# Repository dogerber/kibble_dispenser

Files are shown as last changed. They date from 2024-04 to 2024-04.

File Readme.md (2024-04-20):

# Kibble Dispenser

splash

## Purpose

This device is meant to automatically dispense cat treats to keep cats active during the day. Treats are placed in the small compartments and randomly dispensed within a given time frame.

## Materials

- Arduino UNO
- Adafruit Motorshield V2 (Probably possible without it though)
- 3d Printed parts
- DC Motor
- Power adapter
- [TCRT5000](https://www.bastelgarage.ch/infrarot-sensor-tcrt5000-naherungsschalter-breakout-modul) IR Sensor
- [OLED Display Blau I2c 128x32 0.91’’](https://www.bastelgarage.ch/oled-display-blau-i2c-128x32-0-91?search=ssd13)
- (optional) Buzzer
- resistors, buttons, wires

## How to build

- 3D print all parts from [/dispenser](/dispenser/)
- laser cut and glue enclosure from [/enclosure](/enclosure/)
- install the necessary libraries (see [Dependencies](#dependencies))
- adjust parameters in the code
- wire everything according to [wiring](#wiring)
- upload code/`code.ino`to Arduino Uno
- adjust TCRT5000 potentiometer, such that it triggers when a kibble falls down, but not when something further away moves

### Wiring

- Button 1 to D11 (with pulldown resistor)
- Button 2 to D12 (with pulldown resistor)
- Display to SDA and SCL
- IR sensor TCRT5000 (digital D0) to D2 (used for interrupt)
- (optional) Buzzer to D9
- DC Motor to M1 port of the Motorshield

## How to use

- Update parameters in the code to fit your preferences.
- Manual kibble dispensing is possible with `button2`
- To reset the dispenser push `button1`

## Different Dispensing Mechanisms

To exactly dispense one kibble each time the machine is triggered was harder than expected. For future reference I'm quickly summarizing all the failed approaches here.

(Pictures below)

From top to bottom:

- Final design and only one to work reliably. Unfortunately, the kibbles need to be placed one by one
- Using a feeding wheel like this was very unreliable. It would often not pickup anything
- The auger screw worked sometimes, but often the kibbles would make clogs in the screw that would dispense all together. Redimensioning to make it smaller lead to a lot of jamming problems.
- Inspired by [mint-dispenser](https://www.google.com/url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), in this design a plunger pushes the kibble out and when it moves back a new kibble should fall down. However the kibbles managed to form stable bridges in the dispenser.

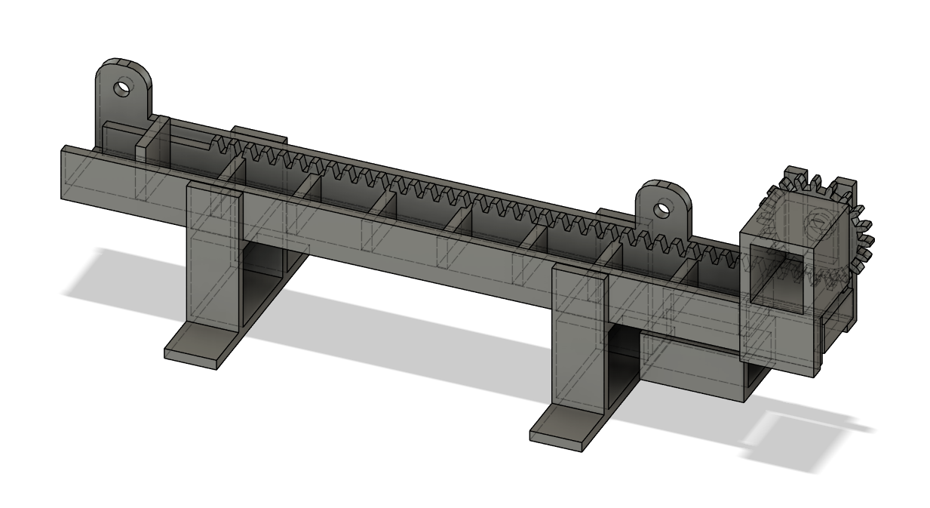
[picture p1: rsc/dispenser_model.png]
rsc/dispenser_model.png|

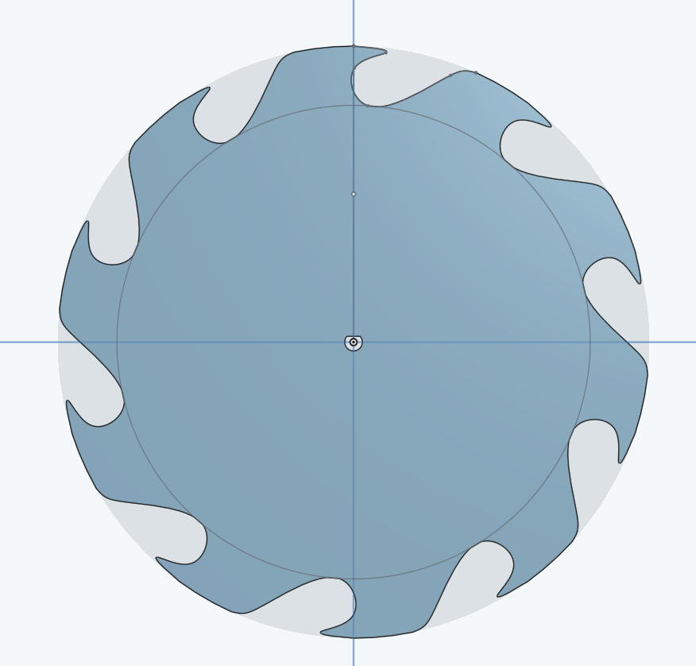
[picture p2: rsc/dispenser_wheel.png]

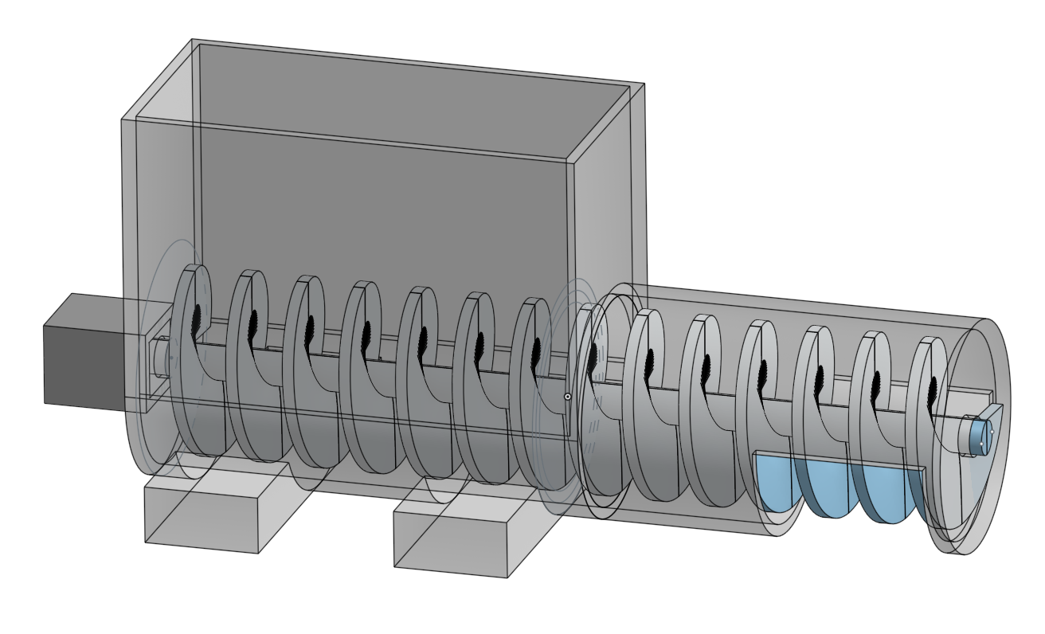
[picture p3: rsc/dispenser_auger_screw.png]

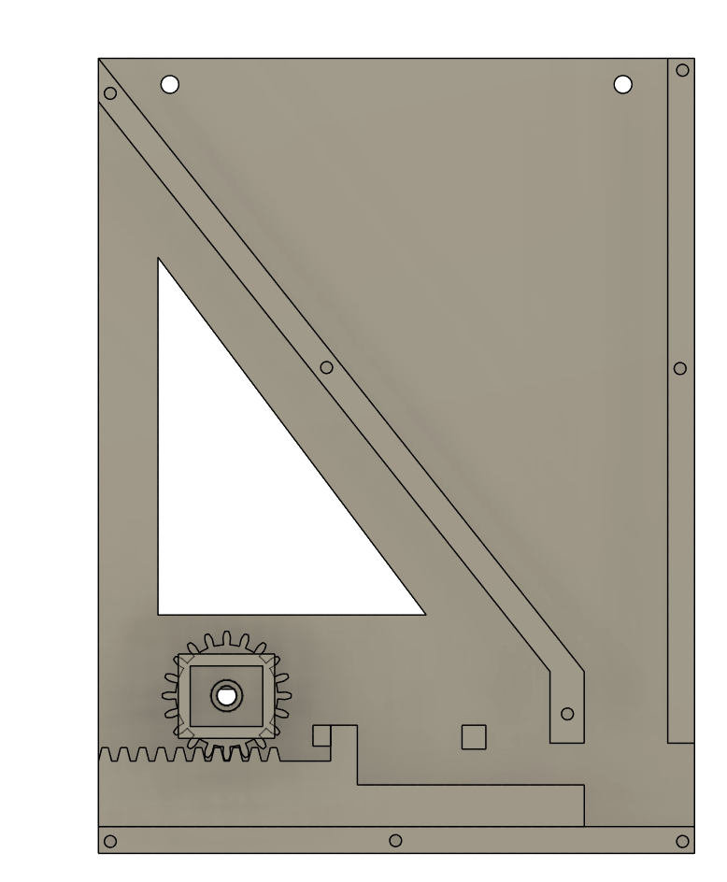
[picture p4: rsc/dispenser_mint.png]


## Dependencies

- [Adafruit Motor Shield v2](https://www.arduino.cc/reference/en/libraries/adafruit-motor-shield-v2-library/)
- [Adafruit_SSD1306]()
- [Adafruit GFX](https://www.arduino.cc/reference/en/libraries/adafruit-gfx-library/)
- [EasyButton.h](https://www.arduino.cc/reference/en/libraries/easybutton/) by Evert Arias

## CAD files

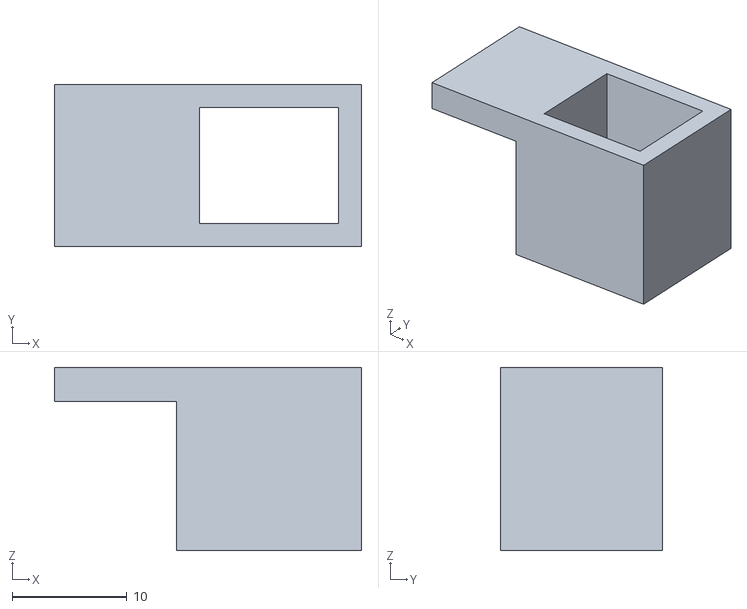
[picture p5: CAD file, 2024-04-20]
dispenser/motor_holder.stl
26.8 x 14.1 x 16.0

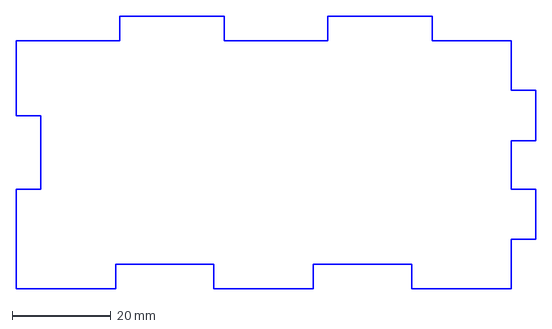
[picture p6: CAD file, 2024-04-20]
enclosure/kibble_dispenser_arduino_box v7 - floor.dxf
105.2 x 55.2 mm

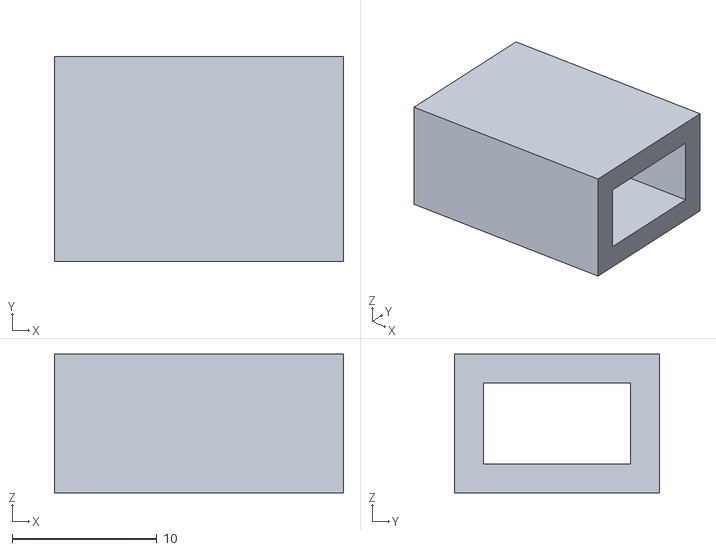
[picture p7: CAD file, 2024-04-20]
dispenser/holder for ir sensor.stl
20.0 x 14.2 x 9.60

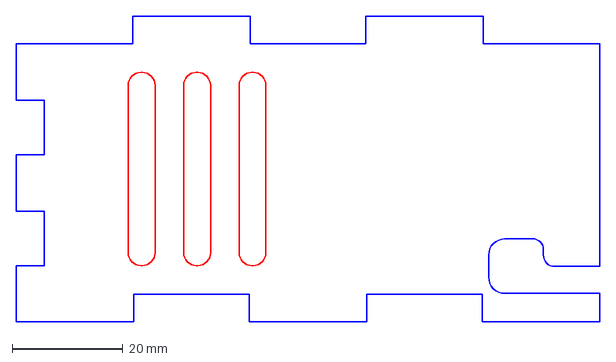
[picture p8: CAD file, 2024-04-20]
enclosure/kibble_dispenser_arduino_box v7 - right_wall.dxf
105.2 x 55.2 mm

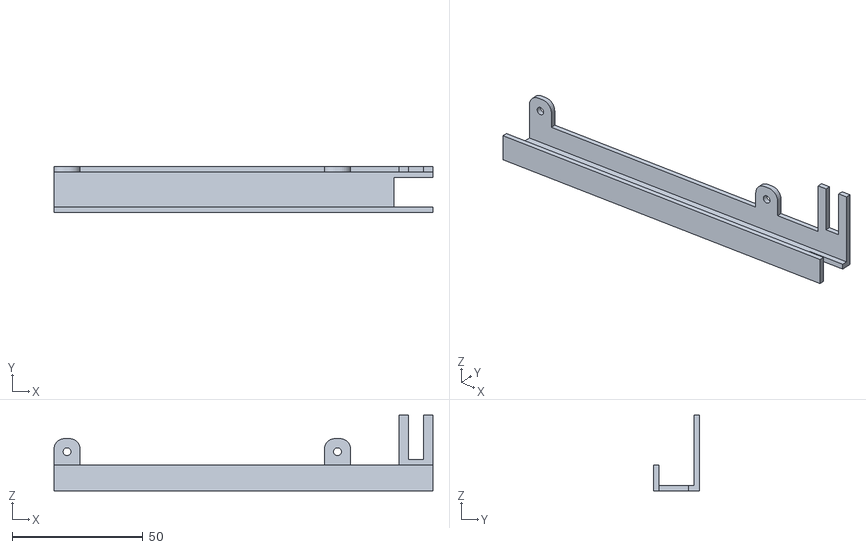
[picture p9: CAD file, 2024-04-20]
dispenser/RAIL.stl
145.0 x 17.5 x 29.0

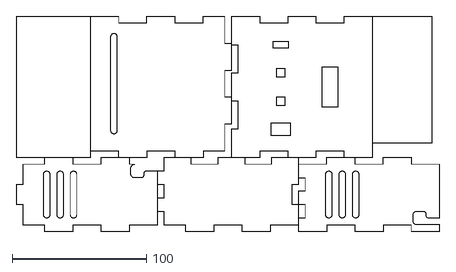
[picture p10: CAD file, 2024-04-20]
enclosure/v1_nested.dxf
315.8 x 160.7

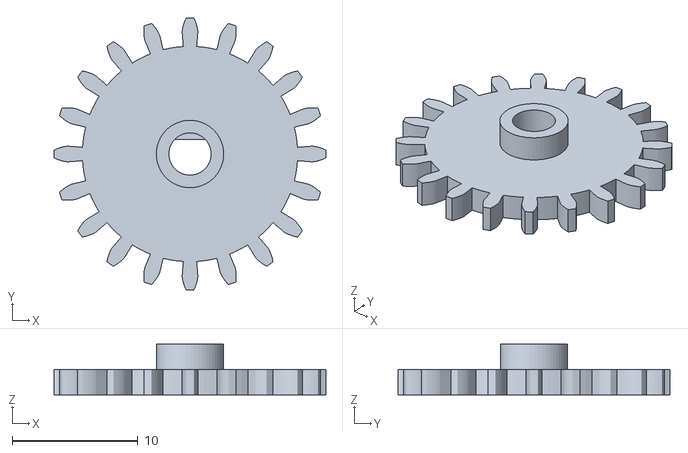
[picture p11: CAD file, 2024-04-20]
dispenser/gear.stl
21.6 x 21.6 x 4.02

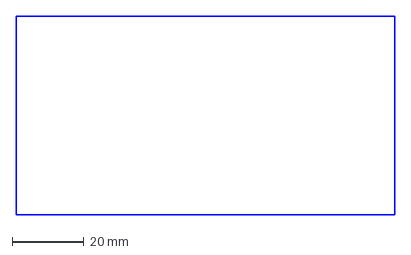
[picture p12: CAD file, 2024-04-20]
enclosure/kibble_dispenser_arduino_box v7 - lid.dxf
105.2 x 55.2 mm

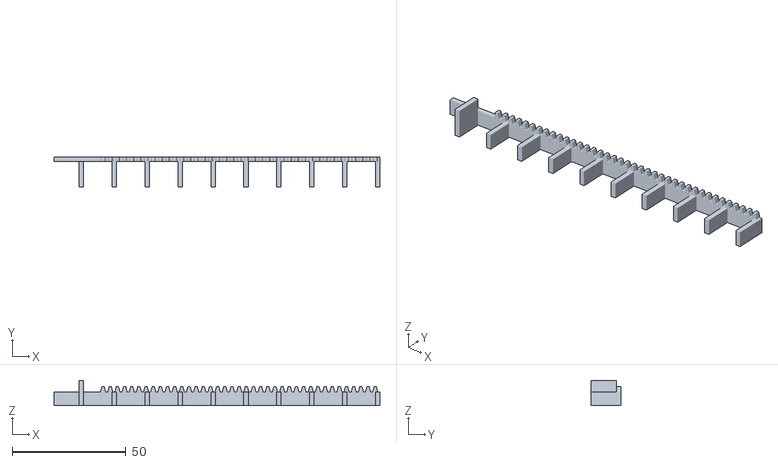
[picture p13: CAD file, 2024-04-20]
dispenser/compartments.stl
143.0 x 13.0 x 11.0

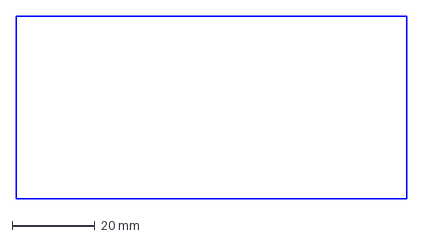
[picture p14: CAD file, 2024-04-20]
enclosure/kibble_dispenser_arduino_box v7 - lid_inside.dxf
94.1 x 44.2 mm

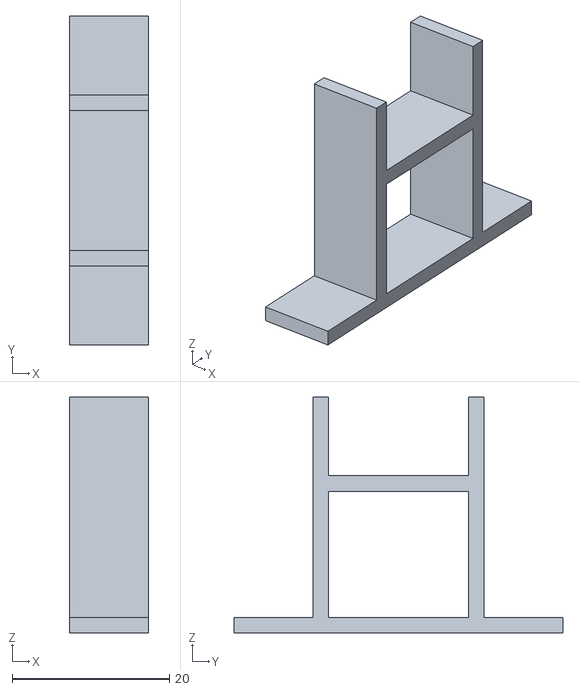
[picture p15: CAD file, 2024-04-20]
dispenser/standfoot.stl
10.0 x 41.8 x 30.0

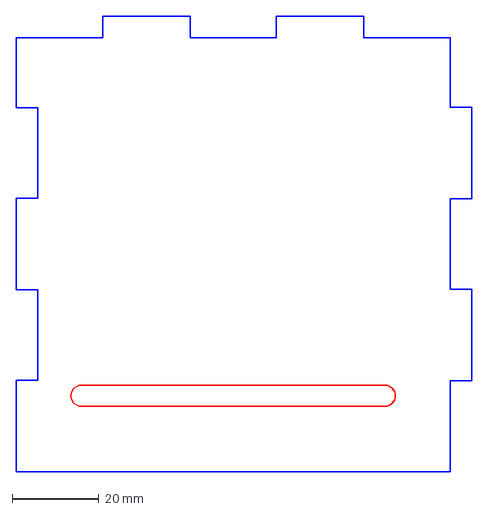
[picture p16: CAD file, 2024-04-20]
enclosure/kibble_dispenser_arduino_box v7 - back_wall.dxf
105.2 x 105.2 mm

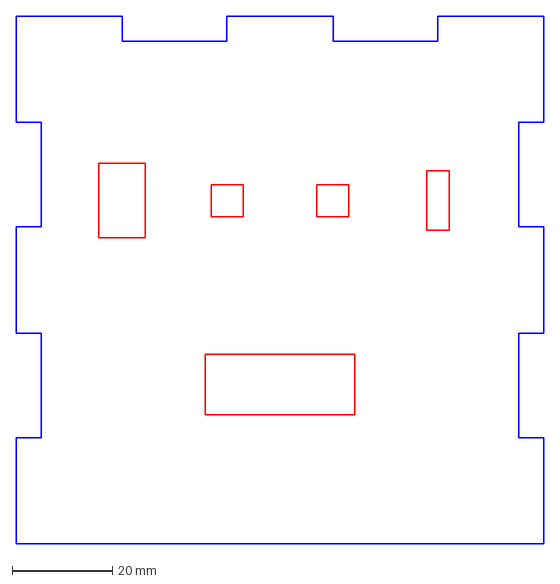
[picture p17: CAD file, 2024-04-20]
enclosure/kibble_dispenser_arduino_box v7 - front wall.dxf
105.2 x 105.2 mm

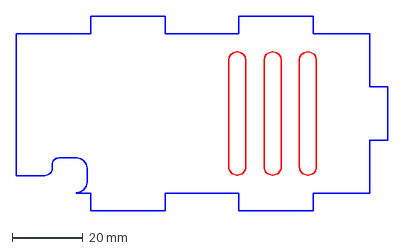
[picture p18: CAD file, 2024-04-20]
enclosure/kibble_dispenser_arduino_box v7 - left_wall.dxf
105.2 x 55.2 mm

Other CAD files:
dispenser/kibble_dispenser_v5 v9.f3d
enclosure/kibble_dispenser_arduino_box v7.f3d

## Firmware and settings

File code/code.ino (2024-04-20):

/*
Kibble Dispenser by Dominic Gerber
https://github.com/dogerber/kibble_dispenser
*/

#define CODE_VERSION "0.1"

#include <Adafruit_MotorShield.h>
#include <EasyButton.h>
#include <SPI.h>              // display
#include <Wire.h>             // display
#include <Adafruit_GFX.h>     // display
#include <Adafruit_SSD1306.h> // display

// Global Parameters
bool do_beep = true;
const unsigned long min_wait_time_ms = 600000;         // [ms] minimum time to wait to dispense
const unsigned long max_wait_time_ms = 3600000;        // [ms] maximum time to wait
const int kibbles_total_available = 9;                 // how many fit into the dispenser [default: 9]
int motor_speed = 90;                                  // [0-255] 0 (off) to 255 (max speed)
const int max_dispenser_timeouts = 2;                  // after this many dispense tries, i stop trying
const unsigned long max_time_dispensing_ms = 6 * 1000; // time after it stops dispensing if no kibble falls out
const int max_time_back_move = 10 * 1000;              // [ms] maximum time of backwards movement (for when triggered by program)//todo reset to 10

// Create the motor shield object with the default I2C address
Adafruit_MotorShield AFMS = Adafruit_MotorShield();
Adafruit_DCMotor *myMotor = AFMS.getMotor(1); // Select which 'port' M1, M2, M3 or M4. In this case, M1

// Display setup
#define SCREEN_WIDTH 128 // OLED display width, in pixels
#define SCREEN_HEIGHT 32 // OLED display height, in pixels

// Declaration for an SSD1306 display connected to I2C (SDA, SCL pins)
// On an Arduino UNO:       A4(SDA), A5(SCL)
#define OLED_RESET -1       // Reset pin # (or -1 if sharing Arduino reset pin)
#define SCREEN_ADDRESS 0x3C ///< See datasheet for Address; 0x3D for 128x64, 0x3C for 128x32
Adafruit_SSD1306 display(SCREEN_WIDTH, SCREEN_HEIGHT, &Wire, OLED_RESET);

// Buttons
#define BUTTON_ONE_PIN 11
#define BUTTON_TWO_PIN 12
EasyButton button1(BUTTON_ONE_PIN);
EasyButton button2(BUTTON_TWO_PIN);

// PINS, Variables
const byte ledPin = 13;
const byte interruptPin = 2; // connected to IR
const int buzzerPin = 9;

// random triggering of dispensing
unsigned long wait_time;

volatile bool change_detected = false;
bool reset_done = false; // this is set true if the machine reset the plunger, waiting to be filled, press green button to confirm filling
volatile bool back_move_toggle = false;
bool back_move_toggle_before = false;
unsigned long time_back_move_started = millis();

int dispenser_timeout_counter = 0;
unsigned long time_last_dispense = 0;

unsigned long time_last_display_refresh = millis();
const int display_refresh_time = 1000 * 1; // refresh rate of screen

int kibbles_dispensed = 0;       // resets when filling dispenser
int kibbles_dispensed_total = 0; // just counts up

/*
Function to dispense a kibble. Once started it is stopped by the IR sensor (which detects a kibble falling down)
Can also be stoped by a timeout (max_time_dispensing_ms) and a button press.
// running like this is bad, as basically it is blocking behaviour.
*/
void dispense_kibble()
{
  time_last_dispense = millis(); // not down when function was last triggered

  // check if kibbles are still available
  if (kibbles_dispensed >= kibbles_total_available)
  {
    // error sound
    if (do_beep)
    {
      tone(buzzerPin, 200);
      delay(200);
      tone(buzzerPin, 200);
      delay(200);
      noTone(buzzerPin);
    }
    return;
  }

  bool do_run = true;
  long time_start = millis();

  // set motorspeed
  myMotor->setSpeed(motor_speed);
  int motor_speed_i = motor_speed;
  int count = 0;

  while (do_run)
  {
    myMotor->run(FORWARD);

    if (change_detected) // succesfull dispensed a kibble
    {
      do_run = false;
      change_detected = false;
      kibbles_dispensed++;
      kibbles_dispensed_total++;
      dispenser_timeout_counter = 0;
    }

    // button1 pressed, abort
    if ((time_start - millis() > 100) &&
        (!button1.read()))
    {
      do_run = false;
    }

    // timeout
    if (millis() - time_start > max_time_dispensing_ms)
    {
      do_run = false;
      dispenser_timeout_counter++;
      if (do_beep)
      {
        tone(buzzerPin, 500);
        delay(200);
        noTone(buzzerPin);
      }
    }
  }

  // stop motor
  myMotor->run(RELEASE);
  if (do_beep)
  {
    tone(buzzerPin, 100);
    delay(100);
    noTone(buzzerPin);
  }
}

void check_ir_led()
{
  // ISP, intterupt function
  change_detected = true;
}

// orange button
void onButton2Pressed()
{
  dispense_kibble(); // it would be better to not do this, because this is blocking behaviour
}

// green button
void onButton1Pressed()
{
  if (reset_done)
  {
    kibbles_dispensed = 0;
    dispenser_timeout_counter = 0;
    reset_done = false;
  }
  else
  {
    back_move_toggle = !back_move_toggle;
    kibbles_dispensed = 0; // reset counter, as now the user should have filled the dispenser
    dispenser_timeout_counter = 0;
  }
}

void setup()
{
  Serial.begin(115200); // set up Serial library at 9600 bps
  Serial.print("kibble_dispenser_code.ino started, v");
  Serial.println(CODE_VERSION);

  // init randomseed
  randomSeed(analogRead(1));
  wait_time = random(min_wait_time_ms, max_wait_time_ms);

  // ----- PIN setups
  pinMode(buzzerPin, OUTPUT);
  pinMode(ledPin, OUTPUT);

  // Interrupts for IR sensor
  pinMode(interruptPin, INPUT_PULLUP);
  attachInterrupt(digitalPinToInterrupt(interruptPin), check_ir_led, FALLING); // was RISING

  // --- Motor stuff
  if (!AFMS.begin())
  { // create with the default frequency 1.6KHz
    // if (!AFMS.begin(1000)) {  // OR with a different frequency, say 1KHz
    Serial.println("Could not find Motor Shield. Check wiring.");
    while (1)
      ;
  }
  Serial.println("Motor Shield found.");

  // init display
  // SSD1306_SWITCHCAPVCC = generate display voltage from 3.3V internally
  if (!display.begin(SSD1306_SWITCHCAPVCC, SCREEN_ADDRESS))
  {
    Serial.println(F("SSD1306 allocation failed"));
    for (;;)
      ; // Don't proceed, loop forever
  }

  if (true)
  { // welcome message
    display.clearDisplay();
    display.setTextSize(1);              // Normal 1:1 pixel scale
    display.setTextColor(SSD1306_WHITE); // Draw white text
    display.setCursor(0, 0);             // Start at top-left corner
    display.print("kibble_dispenser v");
    display.print(CODE_VERSION);
    display.display();
    delay(1000); // Pause for 2 seconds
  }

  // Clear the buffer
  display.clearDisplay();

  // Set the speed to start, from 0 (off) to 255 (max speed)
  myMotor->setSpeed(motor_speed);
  myMotor->run(FORWARD);
  // turn on motor
  myMotor->run(RELEASE);

  // Initialize buttons
  button1.begin();
  button2.begin();
  button1.onPressed(onButton1Pressed);
  button2.onPressed(onButton2Pressed);

  // Initialize Variables
  time_last_dispense = millis();

  // end of setup sound
  if (do_beep)
  {
    tone(buzzerPin, 500); // Sende 1KHz Tonsignal
    delay(100);
    tone(buzzerPin, 1000); // Sende 1KHz Tonsignal
    delay(100);
    noTone(buzzerPin);
  }
}

void loop()
{

  // Continuously read the status of the buttons
  button1.read();
  button2.read();

  // debugging output
  if (true && (millis() % 50) == 0)
  {
    char buff[128];
    // sprintf(buff, "back_move_toggle %d, kibbles_dispensed: %d", back_move_toggle, kibbles_dispensed);
    // Serial.println(buff);
    // sprintf(buff, "millis() %d, millis() - time_back_move_started %d, time_back_move_started %d,", millis(), millis() - time_back_move_started, time_back_move_started);
    // Serial.println(buff);
    sprintf(buff, "time_last_dispense %lu, ((millis() - time_last_dispense))  %lu, wait_time %lu, wait_time/1000 %lu,", time_last_dispense, ((millis() - time_last_dispense)), wait_time, wait_time / 1000);
    Serial.println(buff);
  }

  // add random triggering of the dispenser
  if ((kibbles_dispensed < kibbles_total_available) && (millis() - time_last_dispense > wait_time) && (dispenser_timeout_counter < max_dispenser_timeouts))
  {
    dispense_kibble();
    wait_time = random(min_wait_time_ms, max_wait_time_ms); // determine new wait time
  }

  // update display
  if (millis() - time_last_display_refresh > display_refresh_time)
  {
    display.clearDisplay();
    display.setTextSize(1); // Normal 1:1 pixel scale
    display.setTextColor(SSD1306_WHITE);
    display.setCursor(0, 0);
    char buff[128];

    // tell user to refill
    if (reset_done)
    {
      display.print("REFILL\n Press Green Button \n after filling");
    }
    else if (dispenser_timeout_counter >= max_dispenser_timeouts)
    {
      display.print("FAILED TO DISPENSE\n MULTIPLE TIMES\n Press Green to reset");
    }
    else
    {
      sprintf(buff, "disp: %d / %d,\n tot %d \n ", kibbles_dispensed, kibbles_total_available, kibbles_dispensed_total);
      display.print(buff);

      // show time till next auto dispening if (true)
      {
        sprintf(buff, "time: %lu / %lu min ", ((millis() - time_last_dispense)) / 60000, (wait_time) / 60000); // conversion to minutes /60000
        // Serial.println(buff);
        display.print(buff);
      }
    }

    // refresh display
    display.display();
  }

  // check if all dispensed and if so move back
  if ((!reset_done) && (kibbles_dispensed >= kibbles_total_available))
  {
    back_move_toggle = true;
    reset_done = true;
  }

  // move motor back or stop it
  if (back_move_toggle != back_move_toggle_before)
  {                        // motor state needs to be changed
    if (!back_move_toggle) // if already moving, stop the movement
    {
      myMotor->run(RELEASE);
      back_move_toggle_before = false;
    }
    else
    { // start movement
      myMotor->setSpeed(motor_speed);
      myMotor->run(BACKWARD);
      back_move_toggle_before = true;
      time_back_move_started = millis();
    }
  }

  // check for timeout of back movement
  if (back_move_toggle && (millis() - time_back_move_started > max_time_back_move))
  {
    back_move_toggle = false;
  }

  if (change_detected)
  {
    // ir triggered outside of dispense routine
    if (do_beep)
    {
      tone(buzzerPin, 500);
      delay(100);
      noTone(buzzerPin);
    }

    change_detected = false;
  }
}

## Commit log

2024-03-29 styling and adding abort function (works only with green button)
2024-03-29 added screen and fixed time error where i was using int for millis()
    [code.ino]
2024-03-29 first implementation of auto dispense and dispense error counting
    [code.ino]
2024-03-29 fixed random time error and updated screen
    [code.ino]
2024-04-20 added hw parts
    [RAIL.stl, compartments.stl, gear.stl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]
